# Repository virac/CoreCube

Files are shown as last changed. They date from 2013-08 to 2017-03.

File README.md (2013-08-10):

CoreCube
========

OpenScad design for an Hbot Reprap

Current design is to use aluminum extrusions to create a 500mm cube that has approximatly 350mm x 400mm build area. (May be down to 300mm square once complete.)

Current known parts:
	4x 500mm mitsumi aluminum 20x20mm
	9x 460mm mitsumi aluminum 20x20mm
	2x 500mm 10mm dia precision rod (mcmaster carr)
	2x 400mm 10mm dia presision rod (mcmaster carr)
	8x LM10UU linear bearing (ebay)
	12x bearing small ( for belt travel )
	102xish m5 10mm SHCS (socket head cap screw)
	6x m5 30mm SHCS	( for bearing belt travel )
	8x m5 20mm SHCS ( for top to hold down 10mm rod )
	116xish m5 washer
	116xish m5 tslot nut ( or m5 nut with plastic printed adaptor )
	
planned added parts
	8x DryLin R Solid polymer bearing RJM-01-10; replace the LM10UU in the xy axis
	4x 10mm dia precision rod; for z-axis
	alotx m5 SHCS

possible parts
	2x 460mm mitsumi aluminum 20x20mm; added support/mount points on the vertical axis
	2x 220mm mitsumi aluminum 20x20mm; complete the support/add mount points on the bottom
	
possible problems so far
	the plastic tslot nuts that i am using may not hold the stress from the GT2 belt once tightend

problem found so far and overcome
	corexy belt system using 2 shorter belts. complicated the design. Having to have the 2 belt systems on 2 separate levels when deigning the parts in openscad was overly complicated teying to maintain parametricness. redesigned to only use a single belt after sourcing a long enough single belt from sdp-si
	x-ends no aligning correctly with extension and bearing stop. placed bearings ontop of each other and bearings lined up better, still not perfect; cause is bearing housing is built along the axis of motion so any z-wobble found in the building device will compound the error, may redesign again

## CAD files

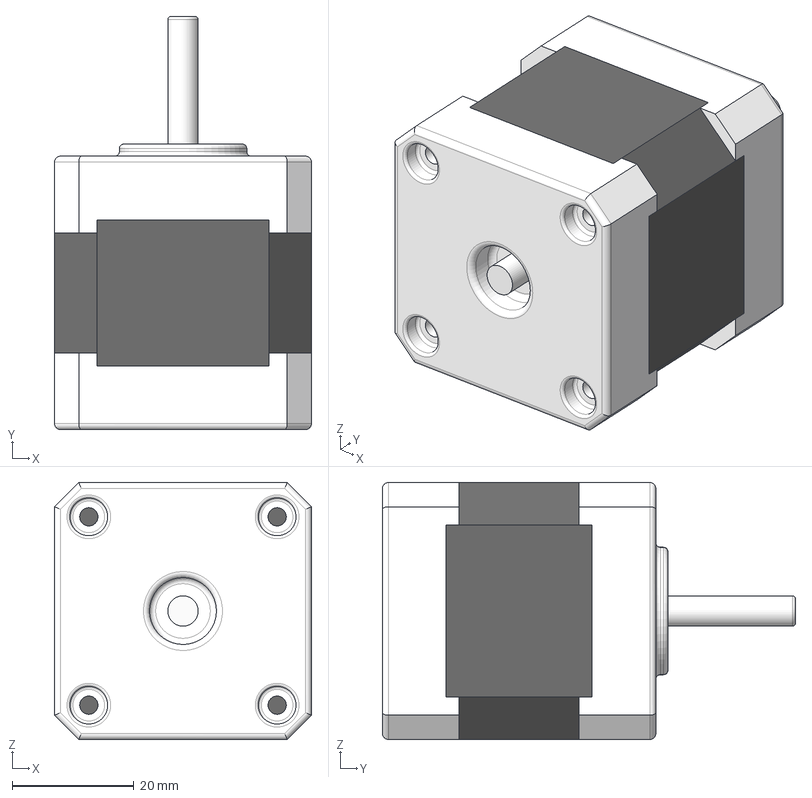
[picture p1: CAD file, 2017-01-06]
CubifyDesign/Nema 17.stp
42.3 x 68.0 x 42.3 mm

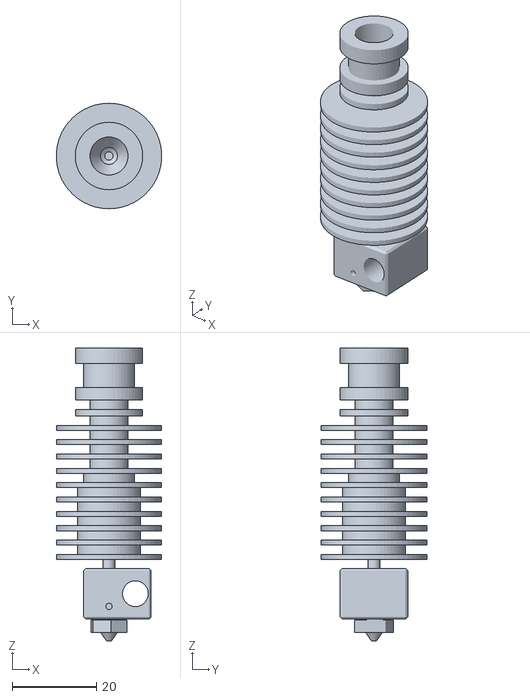
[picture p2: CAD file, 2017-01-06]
E3D_Hot_end.stl
25.0 x 25.0 x 69.4

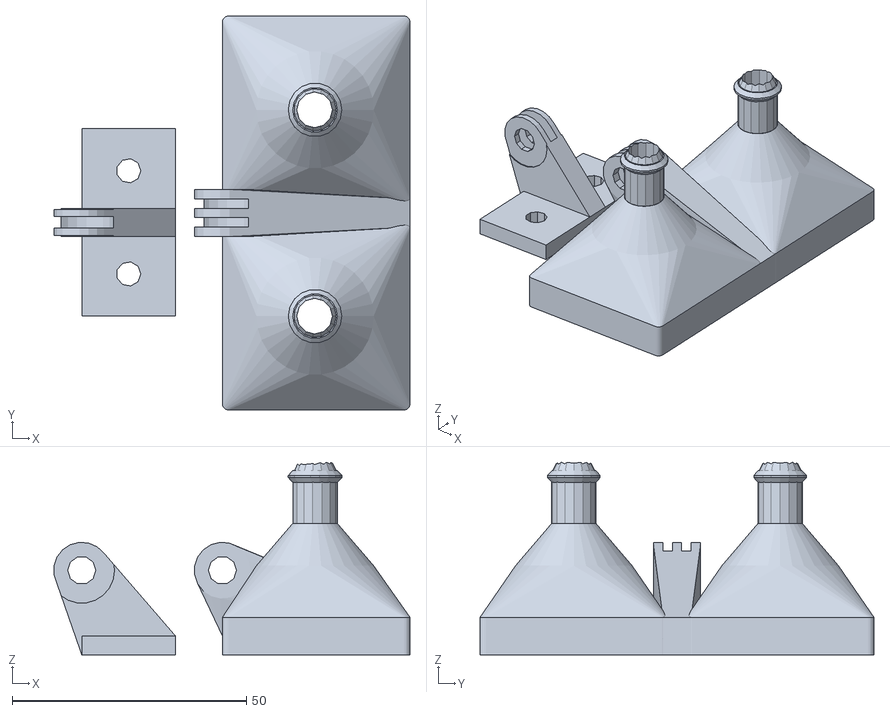
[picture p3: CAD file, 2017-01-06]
STL/snorkel_fan_adapter.stl
75.9 x 84.0 x 41.1

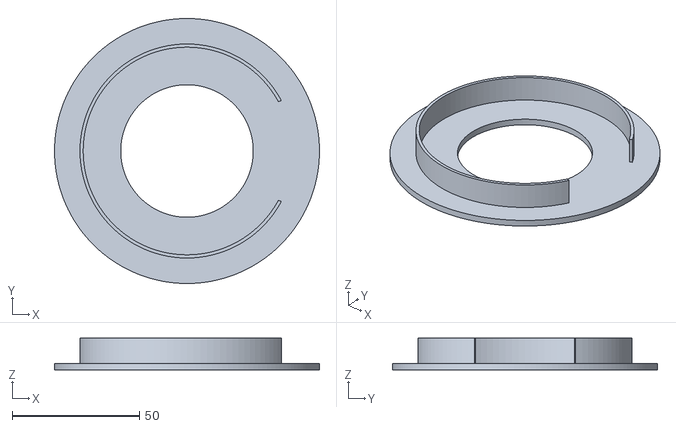
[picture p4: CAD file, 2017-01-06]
STL/adapter_ring.stl
104.0 x 104.0 x 12.5

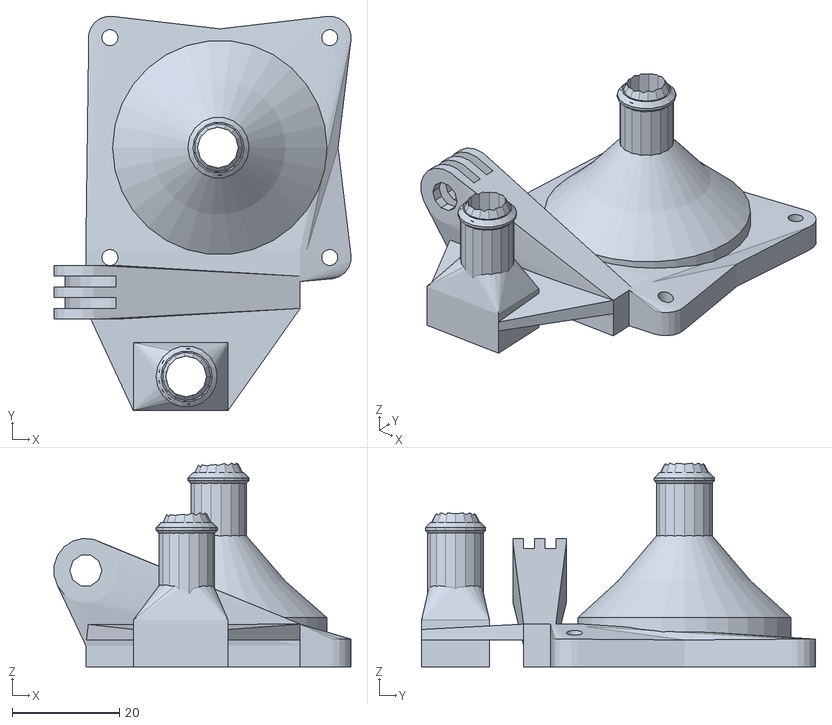
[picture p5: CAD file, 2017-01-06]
STL/snorkel_fan_adapter2.stl
55.4 x 73.5 x 38.1

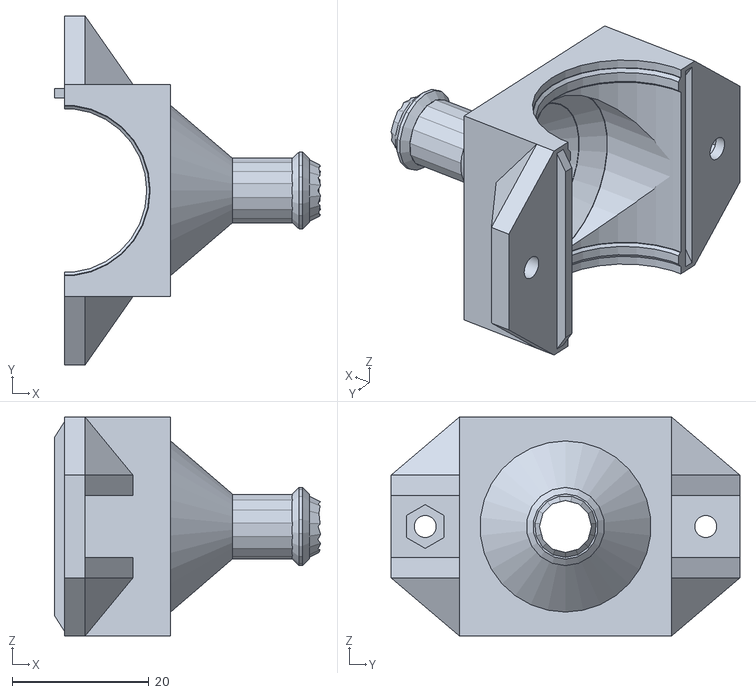
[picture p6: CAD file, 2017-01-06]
STL/snorkel_cooler.stl
38.9 x 51.0 x 32.0

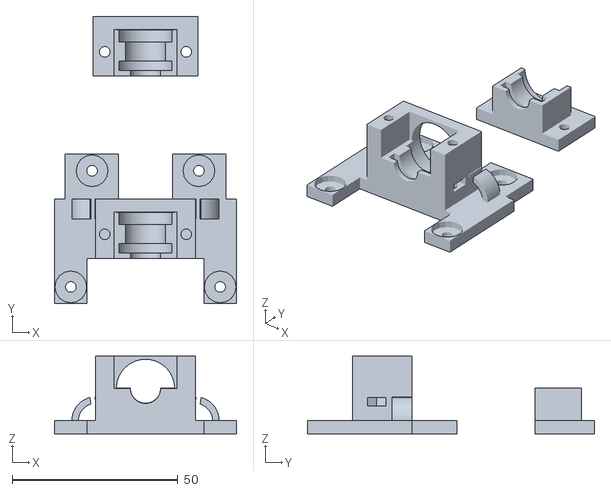
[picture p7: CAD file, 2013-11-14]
STL/mount-jhead.stl
55.0 x 86.5 x 23.5

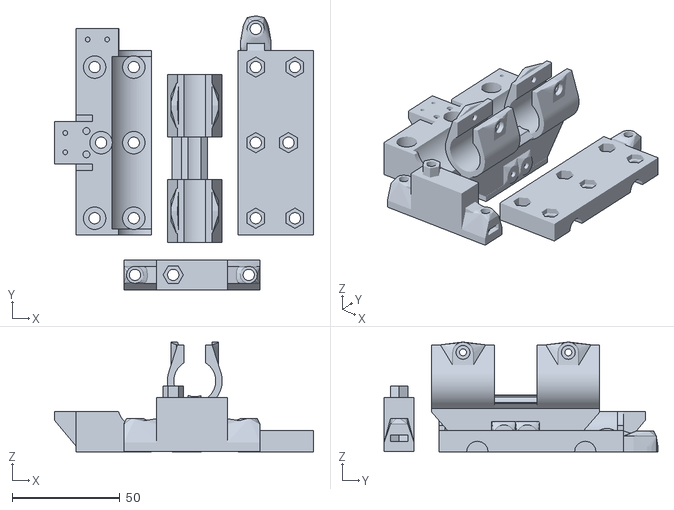
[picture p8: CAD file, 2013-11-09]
STL/x_end_horiz.stl
120.0 x 126.9 x 51.0

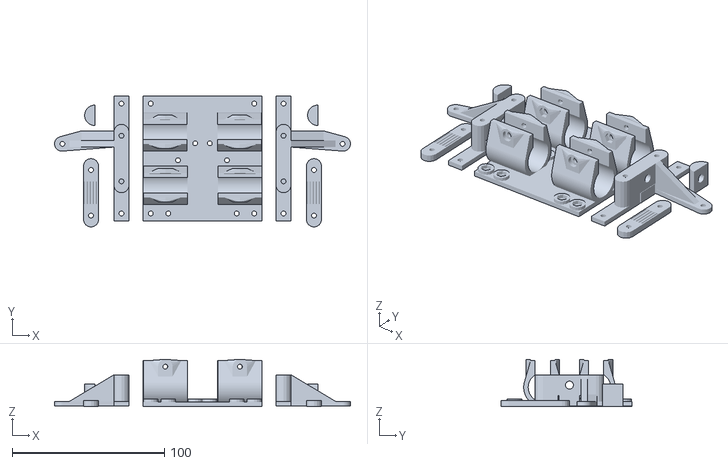
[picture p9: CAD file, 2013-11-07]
STL/carriage.stl
194.5 x 86.1 x 31.1

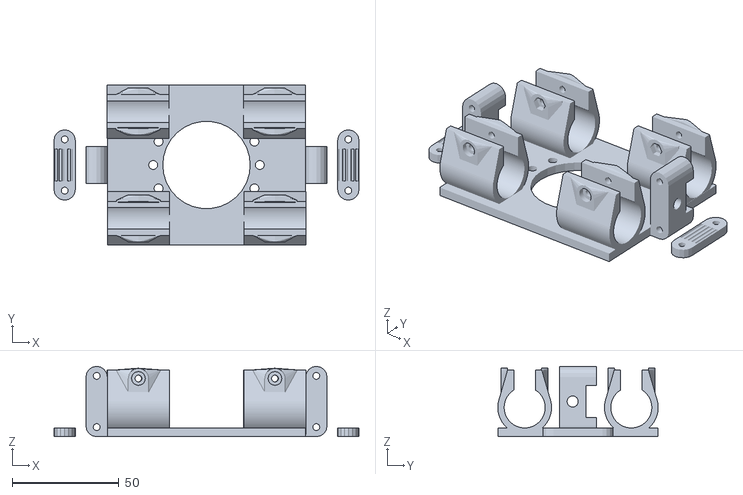
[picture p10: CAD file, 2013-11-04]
STL/carriage_horiz.stl
143.0 x 75.2 x 33.0

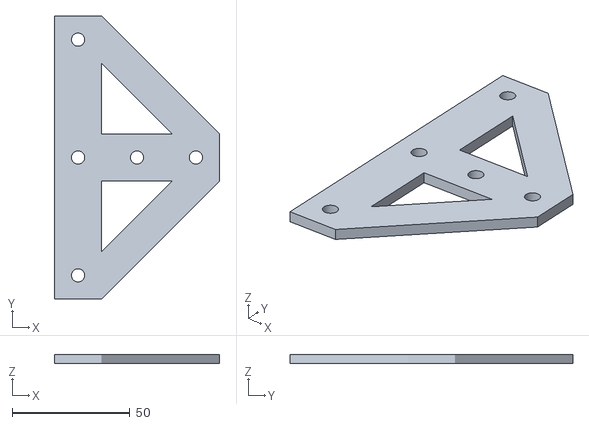
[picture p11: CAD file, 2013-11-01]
STL/side_T_bracket.stl
70.0 x 120.0 x 4.00

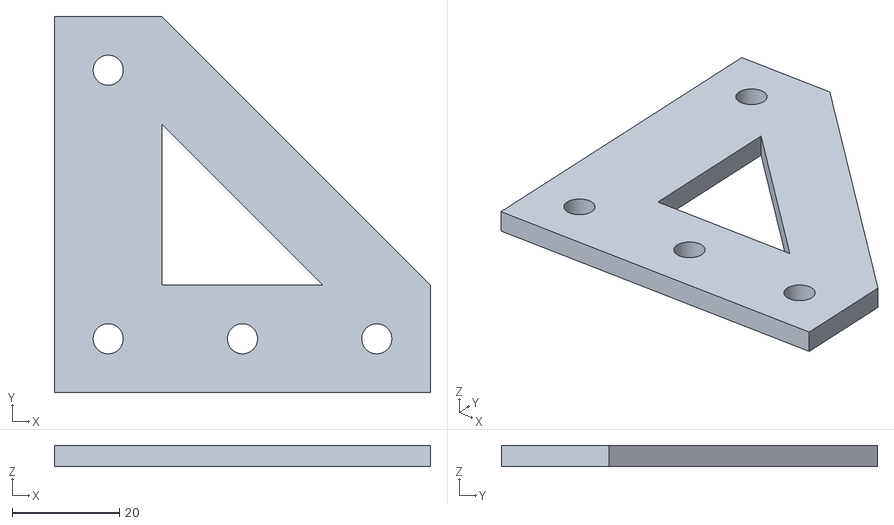
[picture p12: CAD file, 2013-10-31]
STL/corner_bracket.stl
70.0 x 70.0 x 4.00

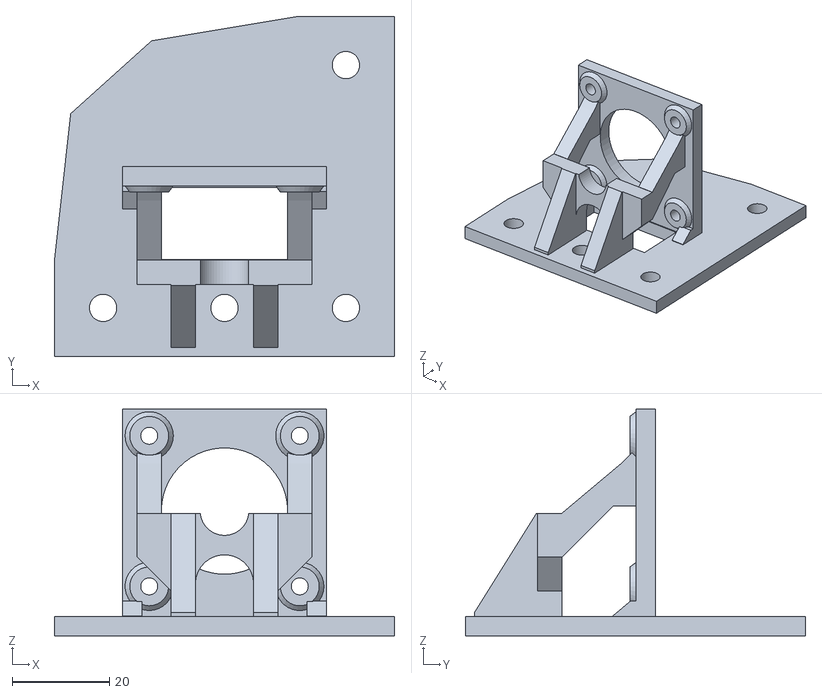
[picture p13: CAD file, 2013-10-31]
STL/corner_motor_bracket.stl
70.0 x 70.0 x 46.7

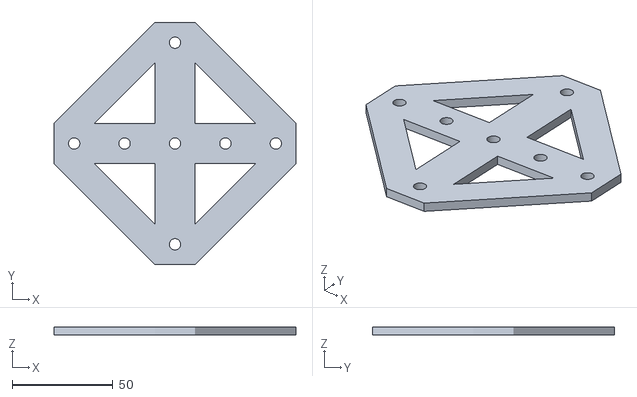
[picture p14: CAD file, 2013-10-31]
STL/bottom_center_bracket.stl
120.0 x 120.0 x 4.00

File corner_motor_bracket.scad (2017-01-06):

include <utils.scad>

show_motor = false;

frame_width = 20;
bracket_length = 70;
bracket_thickness = 4;

nema_l=71.5; // Stepper total length
nema_x=42;
nema_y=42;
nema_z=47.4;
screw_l=30;


for( i = [0,1] )  {
	if( i == 1) {
		mirror([1,0,0]) translate([frame_width*2,0,0])
		corner_motor_bracket( 0 );
	} else {
		//corner_motor_bracket( 0 );
	}
}

module corner_motor_bracket( offset=0 ) {
	union() {
		non_braced_4_hole_L_bracket(frame_width,bracket_length, bracket_thickness);

		motor_brace(frame_width,bracket_length, bracket_thickness,nema_l/3+frame_width/4-frame_width/2-bracket_thickness, offset );

		translate([(bracket_length-frame_width)/2,nema_l/3+frame_width/4+offset,nema_z/2]) rotate([90,0,0])
			nema17_mount();

		if( show_motor == true ) {
			translate([(bracket_length-frame_width)/2,nema_l+frame_width/4,nema_z/2]) rotate([90,0,0]) 
			union() {
				nema17();
				translate([0,0,nema_l-2]) bearing(5, 10, 4);
			}
		}
	}
}
// #########################################################
module nema17_mount() {

	difference () {
		union() {
			translate([0,0,1.7]) cube([nema_x,nema_y,bracket_thickness], center = true);
			translate([0,-3,1.7]) cube([nema_x,nema_y,bracket_thickness], center = true);

			difference() {
				translate([nema_x/2,-nema_y/2-1.5,bracket_thickness-.5]) rotate([0,-90,0]) cube([bracket_thickness*2.5/2,bracket_thickness,bracket_thickness]);
				translate([nema_x/2+1,-nema_y/2-1,bracket_thickness+5]) rotate([0,-90,0]) rotate([0,0,50]) cube([7,7,7]);
			}
			difference() {
				translate([-nema_x/2+bracket_thickness,-nema_y/2-1.5,bracket_thickness-.5]) rotate([0,-90,0]) cube([bracket_thickness*2.5/2,bracket_thickness,bracket_thickness]);
				translate([-nema_x/2+bracket_thickness+1,-nema_y/2-1,bracket_thickness+5]) rotate([0,-90,0]) rotate([0,0,50]) cube([7,7,7]);
			}


			for(r=[1:4]) {
				rotate([0,0,r*360/4]) translate([15.5,15.5,3]) cylinder(2,r1=5.5,r2=4, $fs=.1);
			}

			motor_shaft_brace();

		
		}
		
		union() {

			translate([0,0,2]) cylinder(5,r=13, $fn=50, center = true);	// rev. 3
			translate([0,0,9.8]) cylinder(420,r =5, $fn=50, center = true);	// rev. 3

			for(r=[1:4]) {
				rotate([0,0,r*360/4]) translate([15.5,15.5,-1]) cylinder(40,r=1.75, $fs=.1);
			}
		}
	}
}
module motor_shaft_brace() {
	union() {
		difference() {
			translate([0,-13,21.5]) cube([14,25,5],center=true);
			translate([0,-15,18]) cylinder(7, r = 6, $fs=0.1);
			translate([0,-21,18]) cylinder(7, r = 6, $fs=0.1);
			translate([0,-22,18]) cylinder(7, r = 6, $fs=0.1);
			translate([0,-19.5,21.5]) cube([12,9,6],center=true);
		}
		difference() {
			translate([11,-25.5,19]) rotate([0,-90,0]) cube([18,25,5]);
			translate([12,-22.5,38]) rotate([0,-90,0]) rotate([0,0,32]) cube([18,28,7]);
		}
		difference() {
			translate([-6,-25.5,19]) rotate([0,-90,0]) cube([18,25,5]);
			translate([-5,-22.5,38]) rotate([0,-90,0]) rotate([0,0,32]) cube([18,28,7]);
		}
		difference() {
			union() {
				translate([-10,-17.5,19]) rotate([0,0,45])  cube([15,18,5]);
				translate([-18,-9.5,19]) rotate([-45,0,0]) translate([0,-2,0]) cube([5,28,5]);
				translate([-18,-9.5,22]) rotate([-50,0,0]) translate([0,4.5,0]) cube([5,24,5]);
				translate([-18,1,9]) rotate([-90,0,0]) translate([0,-2,0]) cube([5,10,5]);
			}
			union() {
				translate([-10,-17.5,19])  cube([15,18,5]);
				translate([-5,-.5,18.9])  rotate([0,0,90]) cube([15,18,6]);
				translate([-10,-24.5,19]) rotate([0,0,45])  cube([5,25,5]);
				translate([-23,-9.5,19]) rotate([-45,0,0]) translate([0,-5,0]) cube([5,28,15]);
			}
		}
		mirror([1,0,0]) difference() {
			union() {
				translate([-10,-17.5,19]) rotate([0,0,45])  cube([15,18,5]);
				translate([-18,-9.5,19]) rotate([-45,0,0]) translate([0,-2,0]) cube([5,28,5]);
				translate([-18,-9.5,22]) rotate([-50,0,0]) translate([0,4.5,0]) cube([5,24,5]);
				translate([-18,1,9]) rotate([-90,0,0]) translate([0,-2,0]) cube([5,10,5]);
			}
			union() {
				translate([-10,-17.5,19])  cube([15,18,5]);
				translate([-5,-.5,18.9])  rotate([0,0,90]) cube([15,18,6]);
				translate([-10,-24.5,19]) rotate([0,0,45])  cube([5,25,5]);
				translate([-23,-9.5,19]) rotate([-45,0,0]) translate([0,-5,0]) cube([5,28,15]);
			}
		}
	}
}

module motor_brace(width, length, thickness,motor_offset,offset) {
	union(){
		translate( [length-width/2,width/2,-thickness/2]) linear_extrude(height = thickness) 
				polygon([ 	[0,-0.1], 
							[-width, -0.1], 
							[-length+width,-0.1],
							[-length+width,offset],
							[-width, offset], 
							[-width, offset + motor_offset], 
							[-length+width, offset+ motor_offset], 
							[-length+width, -2*width+length], 
							[-length+width, -width+length],
							[-width,(-2*width+length)*3/2],
							[-width/2/3,-2*width+length]]);
	}
}

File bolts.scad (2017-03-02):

m2_diameter = 2.2;
m2_nut_diameter = 9999;
m2_nut_thickness = 1.7;
m2_tap_diameter = 9999;

m3_diameter = 3.5 ;
m3_cap_diameter = 5.7 ;
m3_cap_thickness = 3.0 ;
m3_nut_diameter = 6.6 ;
m3_nut_thickness = 2.5 ;
m3_tap_diameter = 2.5 ;
m3_washer_diamter = 6.6 ;

m4_diameter = 4.2 ;
m4_nut_diameter = 7.9 ;
m4_nut_thickness = 2.5 ;
m4_tap_diameter = 3.4 ;

m5_diameter = 5.2 ;
m5_cap_length = 5 ;
m5_nut_diameter = 9.4 ;
m5_nut_thickness = 2.7 ;
m5_tap_diameter = 4.3 ;
m5_washer_diameter = 10.5 ;

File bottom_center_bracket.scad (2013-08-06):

include <utils.scad>

frame_width = 20;
bracket_length = 70;
bracket_thickness = 4;


braced_4_hole_L_bracket(frame_width,bracket_length, bracket_thickness);
scale([1,-1,1]) braced_4_hole_L_bracket(frame_width,bracket_length, bracket_thickness);
scale([-1,1,1]) braced_4_hole_L_bracket(frame_width,bracket_length, bracket_thickness);
scale([-1,-1,1]) braced_4_hole_L_bracket(frame_width,bracket_length, bracket_thickness);

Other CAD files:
STL/bottom_corner_bracket.stl
STL/top_bracket.stl
STL/corner_belt_bracket.stl
STL/x_end_verical.stl
bottom_corner_bracket.scad
HyperCubeXL/HyperCubeMax.scad
Includes/FreeSerif.scad
Includes/font_base.scad
carriage.scad
carriage_horiz.scad
coreXY_cube_v2.scad
coreXY_cube_v3.scad
corner_belt_bracket.scad
corner_bracket.scad
fan_holder_v2.scad
impeller.scad
mount-jhead.scad
side_T_bracket.scad
smps_bracket.scad
snorkel_cooler.scad
snorkel_fan_adapter.scad
top_bracket.scad
tslot_nut.scad
utils.scad
x_end_horiz.scad
x_end_verical.scad
z_support_frame.scad

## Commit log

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2013-08-08 Fix to carriage for broken stl file after generation.
    [carriage.scad]
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2013-08-12 Added mount for the jhead to the carriage.
    This is a separate module because the complexities of what both sides
    are needed to be so both have to have a flat surface in-order to print.
    Still messy and needs cleaned up, as well as having to add a way to
    secure the cap to the mount.
    [mount-jhead.scad]
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2013-08-14 Updated the mount jhead for problems encountered on print.
    Added layer of bridge to the nut traps on the mount. Extended the size
    of the cap so you can more easily remove it when in position. Increased
    size of jhead to account for better fit.
    [bolts.scad, mount-jhead.scad]
2013-08-15 Fixed so carriage and mount should fit together. Carriage just needs belt mounts now.
    [carriage.scad, mount-jhead.scad, utils.scad]
2013-08-16 Changed the sizing on the carriage and fixed error message from linear_bearing_holder.
    [carriage.scad, utils.scad]
2013-08-17 Updated the carriage to add cable brace. Problem is that when lining up parts center hole lines up to where cable goes....
    [carriage.scad]
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2013-08-19 Continuing work on the x-end. Added mount hole to the bearing support.
    Still need to add drill hole and nut traps on the x end block and figure
    out a way to print the bearing support by adding a support structure to
    it, or somthing.
    [utils.scad, x_end.scad]
2013-08-20 Updated extruder model to allow for a larger filament size then the body size, for a bowden pushfit adaptor.
    [mount-jhead.scad]
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2013-08-22 Updated the xend. Stuck on how to mount the mount to the block
    [utils.scad, x_end.scad]
2013-08-23 Removed the belt brace from the carriage and started to add it to the mount.
    [carriage.scad, mount-jhead.scad]
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2013-08-24 Updated. Carriage should be in optimal condition. Mount still needs belt attachments.
    [carriage.scad, mount-jhead.scad]
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2013-08-26 Simplified the nut trap code and moved it to the utils file, replaced the nut traps with the new call. Added an offset to the belt tension.
    [mount-jhead.scad, utils.scad]
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2013-08-29 Moved the belt grips to the carriage file from the main body of the extruder. Also changed the grips from square to round.
    I think this is a better place for them. In event of extruder
    changes/types the belts would not have to be removed.
    [carriage.scad, mount-jhead.scad]
2013-08-30 Fixed size issues with size of the belt tension grips.
    [carriage.scad]
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2013-09-05 Moved code around to let it flow better. (and less remembering where things are)
    [carriage.scad]
2013-09-06 Changed the extruder mount so a 20mm m3 bolt could be used regardless of other parameters.
    [mount-jhead.scad]
2013-09-07 Fixed problem in linear_bearing_holder causing it to render incorectly. Moved the bearing support in the xend to be on level for print.
    [utils.scad, x_end.scad]
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2013-09-09 Added printable support for the xend. Should give support and be easily removed.
    [utils.scad, x_end.scad]
2013-09-10 Modified the xend some to allow for better printing, and cleaned up code some.
    [x_end.scad]
2013-09-11 wrote alittle on the snorkel, almost not really. Fixed some rendering issues in the xend
    [snorkel_cooler.scad, x_end.scad]
2013-09-12 Fixed issue when exporting the model to stl (non-manifold).
    [x_end.scad]
2013-09-13 Fixed issues found when printing the xend linear bearing holder.
    [utils.scad, x_end.scad]
2013-09-14 Problem printing fixes
    Moved drill holes in the carriage to within the part addition section so
    the part could be turned on its side to print better. M3 nut size was
    changed for failed prints on the xend
    [bolts.scad, carriage.scad]
2013-09-14 Fixed problems found when printing.
    Belt grabber was off in the way the belts are grabbed.
    Belt tensioner the thickness of the bottom combined with the extra riser
    for the screws caused the m3x10 bolts to not be able to grab. Also
    shortened the width to match the rest better.
    [carriage.scad]
2013-09-16 Added to the xend
    Added the ability to turn off the printed support structure. Added a
    riser to the bolt holes so a 20mm m3 bolt can be used. Reduced the
    amount of support on the undercarriage.
    [utils.scad, x_end.scad]
2013-09-16 Changes to the linear bearing holder.
    added a smoothing block for the linear bearing risers for the m3 bolts.
    Removed extrenous debug lines.
    [utils.scad]
2013-09-18 Changes to the Xend linear bearing holder.
    Added a way to add an offset to allow for separating the linear bearing
    holders.
    Changed the way the holder clasp is calculated.
    [utils.scad, x_end.scad]
2013-09-19 Extruder changes
    Changes to the extruder so the screws have enough length to catch on the
    bolts.
    [mount-jhead.scad]
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2013-09-20 Carriage update
    Updated the belt grabber code to hopefully get a better match to the
    pulley
    [carriage.scad]
2013-09-21 Updates for snorkel
    Added more code to the snorkel.
    Started designing an impeller for forced air intake for the snorkel.
    [impeller.scad, snorkel_cooler.scad, utils.scad]
2013-09-22 Xend update
    Updated the xend linear bearing holder to have a notch that fits around
    the base to keep the holder aligned. Also changed the bearing holders
    themselves by adding a small gap between the bearings. Printed and
    tested, and seem to work exactly as needed.
    [utils.scad, x_end.scad]
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2013-09-25 Major changes.
    Found that the x axis is not stable once the belts have been tightned
    and short moves pull the axis out of alignment. Appears to be up to
    several mm's of error occur when this happens. Changing the xend to hold
    the rails horizontally instead of vertically.
    [x_end_horiz.scad, x_end_verical.scad]
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2013-09-27 Updated impeller and x_end
    Added fins to the impeller design. Need to make them curve somehow.
    [impeller.scad, x_end_horiz.scad]
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2013-10-05 Added nut trap for connection of the linear beaing to the holder.
    [x_end_horiz.scad]
2013-10-06 Xend horizontal updates
    Added limit switches on both sides of the y axis, made all limit
    switches flag configurable
    Added holes to screw the top and bottom of the rod holder together.
    [bolts.scad, x_end_horiz.scad]
2013-10-06 Xend horiz modification
    Changed the back holes so a 10mm M5 bolt could be used instead of a 15mm
    [x_end_horiz.scad]
2013-10-08 Utils and xend horiz update
    Utils fixed the belt bearing support.
    Xend horiz started to add belt bearing support parts.
    [utils.scad, x_end_horiz.scad]
2013-10-09 Xend changes
    Modified the xend so the back bolts align with the belt bolts, to either
    use them as support anchors or as the travel itself. Using the bolts as
    the anchors may have a problem with the carriage not having enough
    clearance.
    [x_end_horiz.scad]
2013-10-10 Xend update
    Worked on how to have the belts routed. This would work but printing
    would be an issue.
    [x_end_horiz.scad]
2013-10-11 Xend update
    "finished" the xend horiz, code is still ugly and needs cleaned up, belt
    grab needs fixed but want to see if it will work once printed.
    Next up "the carriage horiz"
    [x_end_horiz.scad]
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2013-10-13 Xend updates
    updates to make the xend print better. Still needs cleaned up.
    [x_end_horiz.scad]
2013-10-15 Xend fixes
    Fixed a typo that cause the model to render incorrectly.
    [x_end_horiz.scad]
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2013-10-18 Carriage and snorkel update
    Updated the carriage to position the linear bearings along the sides of
    the carriage, added hole in center. need to figure out some way to
    integrate the hole size with the bearing positioning.
    Added piping to the snorkel, will need to add some way for it to have
    internal supports for printing.
    [carriage_horiz.scad, snorkel_cooler.scad]
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2013-10-23 Xend change
    Changed the depth of the nut in the xend so a 30mm m5 can be used.
    [x_end_horiz.scad]
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2013-10-27 Xend Vert mods
    Tried modifying the Xend Vert to work and maintain stability. Also added
    the STL of the rendered file.
    [utils.scad, x_end_verical.scad, x_end_verical.stl]
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2013-10-30 Mount
    Changed the mount holes to match the carriage and added the STL
    [mount-jhead.scad, mount-jhead.stl]
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2013-11-02 Snorkel
    Updated so there is a fin grip at the top and bottom of the cooler
    [snorkel_cooler.scad, snorkel_cooler.stl]
2013-11-04 Stl updates
    updated the stl for hte carrige horiz with a second belt grabber and the
    xend with z leveling.
    [carriage_horiz.scad, carriage_horiz.stl, x_end_horiz.scad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]
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2013-11-13 Jhead mount
    Moved the wire guides so they are no longer blocking the nut traps.
    [mount-jhead.scad, mount-jhead.stl]
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2014-02-05 Updates
    Tried to correct some of the math, still off but closer.
    [z_support_frame.scad]
2014-02-19 Fixes
    Changed the math to work with points instead of lines, as i was getting
    rounding errors i think. Added min area reduction to.
    [z_support_frame.scad]
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
